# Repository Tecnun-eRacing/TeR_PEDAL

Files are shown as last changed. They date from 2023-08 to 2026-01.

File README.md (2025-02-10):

# TeR_PEDAL
The drivers Input Module Sensor, built to fit FSG rules, it provides the vehicle 
data about:
- Brake Pressure
- APPS (Accelerator Pedal Position Sensor)
- Steering Sensor
## Features
- The module is able to self calibrate itself through a series of commands trough CAN 2.0
- Implausible range detection in all sensors + Safety set-zero
- Storage of calibration values in the internal EEPROM for persistance

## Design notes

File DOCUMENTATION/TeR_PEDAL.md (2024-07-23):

# TeR_PEDAL : Hardware Engineering Report
La placa PEDAL del vehiculo TeR, es la encargada de recopilar todos los inputs que el piloto introduce al coche, Acelerador (APPS), 
Freno Delantero (BPPS) y Volante (STEER). Los datos obtenidos serán utilizados por la ECU para gestionar el par comandado al powertrain.
## Requerimientos
La normativa de FSG tiene una sección (T11.8) que exije los siguientes requerimientos:

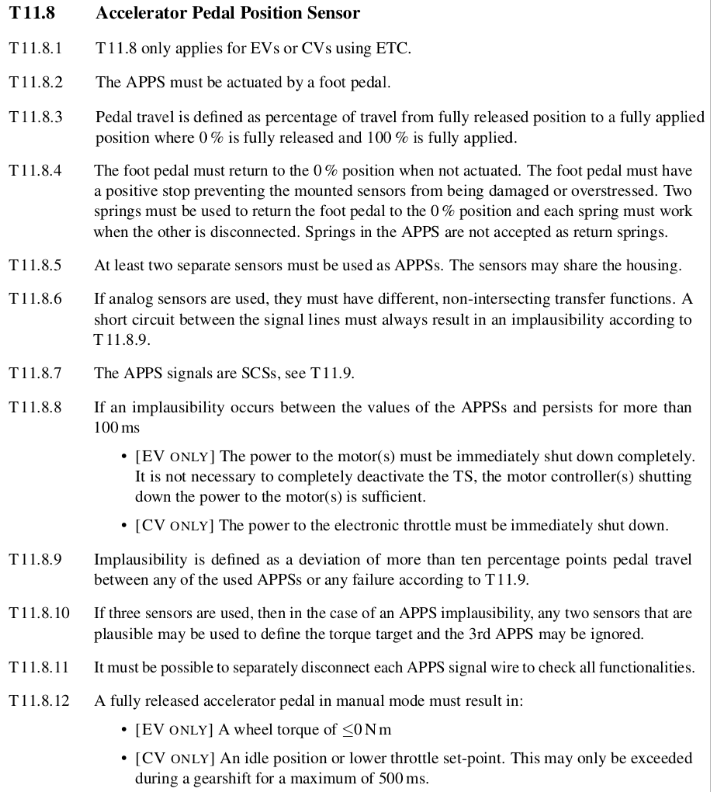
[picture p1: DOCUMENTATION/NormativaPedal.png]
Normativa

## Decisiones

### Sensores
  Por simplicidad y flexibilidad utilizaremos sensores analógicos para la medición de los pedales, steering y freno, cualquier [Potenciometro](https://es.wikipedia.org/wiki/Potenci%C3%B3metro)
  sirve, pero usamos concretamente los VariOhm de Eurosensors

|Fisicamente | Electricamente |
|---|---|
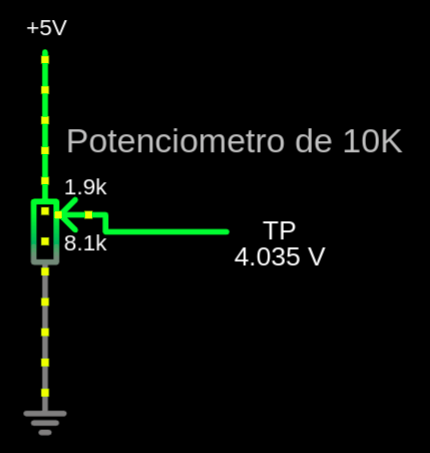
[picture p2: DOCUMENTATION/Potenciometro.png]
Potenciometro
| VariOhm |   |

Para el Freno utilizamos un transductor de Presión-Voltaje que nos permite conocer mediante su función de transferencia la presión en la linea.

### MCU
  Se ha utilizado un stm32F103C8T6 de 48 pines por su facilidad de obtención, versatilidad, disponibilidad de un buen periferico [ADC SAR](https://en.wikipedia.org/wiki/Successive-approximation_ADC) y soporte CAN.
  su uso en la mayoría de placas de baja potencia de procesamiento permite estandarizar y familiarizar todos los diseños donde no se requiere mucha potencia de computo.
  
  | Specification               | Description                          |
  |-----------------------------|--------------------------------------|
  | Core                        | ARM Cortex-M3                        |
  | Operating Frequency         | 72 MHz                               |
  | Flash Memory                | 64 KB                                |
  | RAM                         | 20 KB                                |
  | GPIO                        | 37                                   |
  | Timers                      | 3 x 16-bit, 1 x 32-bit, 2 x watchdog |
  | Communication Interfaces    | 2 x I2C, 3 x USART, 2 x SPI, 1 x USB |
  | ADC                         | 2 x 12-bit, 10-channel               |
  | DAC                         | None                                 |
  | PWM Channels                | 15                                   |
  | Operating Voltage           | 2.0 - 3.6 V                          |
  | Package                     | LQFP48                               |
  | Temperature Range           | -40 to +85 °C                        |
  | Power Consumption (Sleep)   | 2 µA                                 |
  | Debug Interface             | SWD, JTAG                            |
  
  Estos micros se programan muy facilmente mediante el uso de un debugger ST-link y el stm32CUBE-IDE utilizando las librerías [HAL](https://es.wikipedia.org/wiki/Capa_de_abstracci%C3%B3n_de_hardware)

### Filtrado 
Para filtrar las señales recibidas por los sensores se utilizan unos filtros paso bajo RC , pasivos sencillos con frecuencia de corte ~100hz lo cual permite eliminar cualquier señal que 
no provenga del piloto (Sus inputs son mucho más lentos, Fourier...), convendría actualizar a filtros activos utilizando opamps para no afectar las impedancias de entrada.

## Comprobación de requisitos

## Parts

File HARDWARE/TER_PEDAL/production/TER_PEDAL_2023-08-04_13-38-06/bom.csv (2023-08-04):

Designator | Footprint | Quantity | Value | LCSC Part #
C1 | 0805 | 1 | 10u
C10, C9 | 0805 | 2 | 10 µF
C11, C12, C13, C19, C20, C23 | 0603 | 6 | 10u
C14, C17 | 0603 | 2 | 100n
C15, C16 | 0603 | 2 | 10p
C18 | 0603 | 1 | 4.7n
C2, C3, C4, C5 | 0402 | 4 | 100n
C6 | 0402 | 1 | 10n
C7, C8 | 0402 | 2 | 1u
D2 | SOT-23 | 1 | NUP2105L
D3, D4, D5 | 0603 | 3 | LED
F2 | 0805 | 1 | 500ma
FB1, R13, R14, R15 | 0402 | 4 | 120R
J1 | PinHeader_1x04_P2.00mm_Vertical | 1 | DEBUG
J2 | Wuerth_WR-WTB_64800311622_1x03_P1.50mm_Vertical | 1 | APPS_1
J3 | RJ45_Ninigi_GE | 1 | RJ45_Shielded
J4 | Wuerth_WR-WTB_64800311622_1x03_P1.50mm_Vertical | 1 | APPS_2
J5 | Wuerth_WR-WTB_64800311622_1x03_P1.50mm_Vertical | 1 | BPPS_1
J6 | Wuerth_WR-WTB_64800311622_1x03_P1.50mm_Vertical | 1 | SteerSensor
JP1 | PinHeader_1x03_P2.00mm_Vertical | 1 | BOOT0
JP2 | PinHeader_1x03_P2.00mm_Vertical | 1 | BOOT1
JP3 | SolderJumper-3_P1.3mm_Open_Pad1.0x1.5mm | 1 | TermEnable
L1 | IND_TCK-141_TRP | 1 | TCK-141
R10 | 0603 | 1 | 2k
R11 | 0603 | 1 | 4.7k
R12 | 0603 | 1 | 9.1k
R4, R5 | 0603 | 2 | 10k
R6 | 0402 | 1 | 300R
R7 | 0603 | 1 | 100R
R8, R9 | 0603 | 2 | 50R
SW1 | SW_Tactile_SPST_NO_Straight_CK_PTS636Sx25SMTRLFS | 1 | RST
U1 | LQFP-48_7x7mm_P0.5mm | 1 | STM32F103C8Tx
U2 | Converter_DCDC_TRACO_TSR-1_THT | 1 | TSR_1-2450
U3 | SOT-223-3_TabPin2 | 1 | LM1117MP-3.3
U4 | SOIC-8_3.9x4.9mm_P1.27mm | 1 | SN65HVD230
Y1 | Crystal_HC52-6mm_Vertical | 1 | 8mHz

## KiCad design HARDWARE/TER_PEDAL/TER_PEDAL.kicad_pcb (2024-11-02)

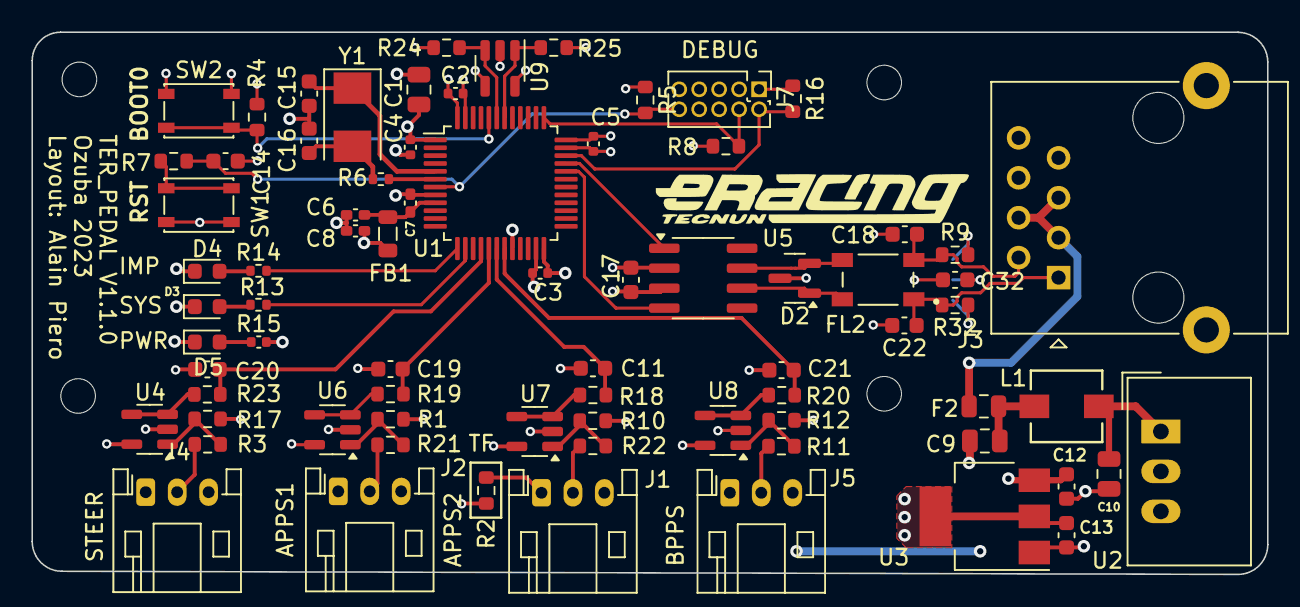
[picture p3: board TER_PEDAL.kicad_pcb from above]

Board: 4 copper layers, 78.6 x 34.5 mm, 80 parts (1 on the bottom side), 48 nets.

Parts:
C1: 10u; C_0805_2012Metric
C2, C3, C4, C5: 100n; C_0402_1005Metric
C6: 10n; C_0402_1005Metric_Pad0.74x0.62mm_HandSolder
C7, C8: 1u; C_0402_1005Metric_Pad0.74x0.62mm_HandSolder
C9, C10: 10 µF; C_0805_2012Metric
C11, C19, C20, C21: 160n; C_0603_1608Metric
C12, C13: 10u; C_0603_1608Metric
C14, C17: 100n; C_0603_1608Metric
C15, C16, C18, C22: 10p; C_0603_1608Metric
C32: 4.7nF; C_0603_1608Metric
D2: NUP2105L; SOT-23
D3: SYS; LED_0603_1608Metric
D4: IMP; LED_0603_1608Metric
D5: PWR; LED_0603_1608Metric
F2: 500ma; Fuse_0805_2012Metric
FB1: 120R; L_0805_2012Metric
FL2: ACT45B-510-2P-TL003; FIL_ACT45B-510-2P-TL003
H1, H2, H3, H4: MountingHole; MountingHole_2.2mm_M2
J1: APPS_2; JST_PH_S3B-PH-K_1x03_P2.00mm_Horizontal
J2, J4: APPS_1; JST_PH_S3B-PH-K_1x03_P2.00mm_Horizontal
J3: RJ45_Shielded; RJ45_Ninigi_GE
J5: BPPS_1; JST_PH_S3B-PH-K_1x03_P2.00mm_Horizontal
J7: DEBUG; PinHeader_2x05_P1.27mm_Vertical
JP2: SolderJumper_3_Open; SolderJumper-3_P1.3mm_Open_Pad1.0x1.5mm
L1: TCK-141; IND_TCK-141_TRP
R1, R10, R12, R17: 9.1k; R_0603_1608Metric
R2: 0R; R_0603_1608Metric
R3, R11, R21, R22: 4.7k; R_0603_1608Metric
R4, R24, R25: 10k; R_0603_1608Metric
R5, R8, R16: 100k; R_0603_1608Metric
R6: 300R; R_0402_1005Metric
R7: 100R; R_0603_1608Metric
R9, R32: 120R; R_0603_1608Metric
R13, R14: 120R; R_0402_1005Metric
R15: 120R; C_0402_1005Metric
R18, R19, R20, R23: 100; R_0603_1608Metric
SW1: RST; SW_SPST_PTS810
SW2: BOOT0; SW_SPST_PTS810
U1: STM32F103C8Tx; LQFP-48_7x7mm_P0.5mm
U2: TSR_1-2450; Converter_DCDC_TRACO_TSR-1_THT
U3: LM1117MP-3.3; SOT-223-3_TabPin2
U4, U6, U7, U8: LM321; SOT-23-5
U5: TCAN332; SOIC-8_3.9x4.9mm_P1.27mm
U9: AT24CS02-STUM; SOT-23-5
Y1: 8mHz; Crystal_SMD_5032-2Pin_5.0x3.2mm

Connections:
+3.3V: C1.1, C2.1, C3.1, C4.1, C5.1, C8.1, C13.1, C17.2, FB1.2, J7.1 (VTref), R5.1, R15.2, R16.1, R24.1, R25.1, SW2.2 (B), U1.1 (VBAT), U1.24 (VDD), U1.36 (VDD), U1.48 (VDD), U3.2 (VO), U4.5 (V+), U5.3 (VCC), U6.5 (V+), U7.5 (V+), U8.5 (V+), U9.4 (VCC)
+3.3VADC: C6.1, C7.1, FB1.1, U1.9 (VDDA)
+5V: C12.1, J2.1, J4.1, J5.1, R2.1, U2.3 (Vout), U3.3 (VI)
+24V: F2.1, J3.3, J3.4, J3.5
/CAN/CAN+: C18.2, FL2.2, J3.2, R9.1
/CAN/CAN-: C22.1, FL2.1, J3.1, R32.2
/CAN/CAN_RX: U1.32 (PA11), U5.4 (RXD)
/CAN/CAN_TX: U1.33 (PA12), U5.1 (TXD)
/CAN/can+: D2.2 (K), FL2.3, U5.7 (CANH)
/CAN/can-: D2.1 (K), FL2.4, U5.6 (CANL)
/EEPROM/SCL: R25.2, U1.42 (PB6), U9.1 (SCL)
/EEPROM/SDA: R24.2, U1.43 (PB7), U9.3 (SDA)
/IMP_LED: R14.2, U1.13 (PA3)
/MICRO/APPS_1_ADC: C19.1, R19.2, U1.17 (PA7)
/MICRO/APPS_2_ADC: C11.1, R18.2, U1.18 (PB0)
/MICRO/BOOT0: R4.1, SW2.1 (A), U1.44 (BOOT0)
/MICRO/BPPS_ADC: C21.1, R20.2, U1.19 (PB1)
/MICRO/NRST: C14.1, J7.10 (~RESET), R5.2, R7.2, U1.7 (NRST)
/MICRO/OSC_IN: C15.2, U1.5 (PD0), Y1.1
/MICRO/OSC_OUT: R6.1, U1.6 (PD1)
/MICRO/STEER_ADC: C20.1, R23.2, U1.16 (PA6)
/MICRO/SWCLK: J7.4 (SWCLK/TCK), R8.1, U1.37 (PA14)
/MICRO/SWDIO: J7.2 (SWDIO/TMS), R16.2, U1.34 (PA13)
/SENSORS/Brake: J5.2, R11.1
/SENSORS/SENS_1: J2.2, R21.2
/SENSORS/SENS_2: J1.2, R22.2
/SYS: R13.2, U1.14 (PA4)
GND: C1.2, C2.2, C3.2, C4.2, C5.2, C6.2, C7.2, C8.2, C9.2, C10.2, C11.2, C12.2, C13.2, C14.2, C15.1, C16.2, C17.1, C18.1, C19.2, C20.2, C21.2, C22.2, C32.2, D2.3 (A), D3.1 (K), D4.1 (K), D5.1 (K), J1.3, J2.3, J3.6, J3.7, J3.8, J3.SH, J4.3, J5.3, J7.3 (GND), J7.5 (GND), J7.9 (GNDDetect), R1.1, R4.2, R8.2, R10.1, R12.2, R17.1, SW1.1 (A), U1.8 (VSSA), U1.20 (PB2), U1.23 (VSS), U1.35 (VSS), U1.47 (VSS), U2.2 (GND), U3.1 (GND), U4.2 (V-), U5.2 (GND), U6.2 (V-), U7.2 (V-), U8.2 (V-), U9.2 (GND), U9.5 (WP)
unnamed: C9.1, F2.2, L1.2
unnamed: C16.1, R6.2, Y1.2
unnamed: D3.2 (A), R13.1
unnamed: D4.2 (A), R14.1
unnamed: D5.2 (A), R15.1
unnamed: J1.1, R2.2
unnamed: J4.2, R3.2
unnamed: JP2.1 (A), R9.2
unnamed: JP2.3 (B), R32.1
unnamed: C32.1, JP2.2 (C)
unnamed: R7.1, SW1.2 (B)
unnamed: C10.1, L1.1, U2.1 (Vin)
unnamed: R3.1, R17.2, U4.1 (+)
unnamed: R23.1, U4.3 (-), U4.4
unnamed: R1.2, R21.1, U6.1 (+)
unnamed: R19.1, U6.3 (-), U6.4
unnamed: R10.2, R22.1, U7.1 (+)
unnamed: R18.1, U7.3 (-), U7.4
unnamed: R11.2, R12.1, U8.1 (+)
unnamed: R20.1, U8.3 (-), U8.4

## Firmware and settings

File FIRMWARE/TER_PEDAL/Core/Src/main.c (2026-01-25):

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
/* Includes ------------------------------------------------------------------*/
#include "main.h"
#include "adc.h"
#include "can.h"
#include "dma.h"
#include "i2c.h"
#include "tim.h"
#include "gpio.h"

/* USER CODE BEGIN Includes */
#include "TeR_CAN.h" //Master libray
#include "pedal.h" //Board functions Library
/* USER CODE END Includes */


/* USER CODE BEGIN PV */
EE24_HandleTypeDef ee24;

//Mensajes

/* USER CODE END PV */

void SystemClock_Config(void);
static void MX_NVIC_Init(void);
/* USER CODE BEGIN PFP */
void readSensors(void); //Lectura de todos los sensores

/* USER CODE END PFP */

/**
 * @brief  The application entry point.
 * @retval int
 */
int main(void) {

	/* MCU Configuration--------------------------------------------------------*/

	/* Reset of all peripherals, Initializes the Flash interface and the Systick. */
	HAL_Init();

	/* Configure the system clock */
	SystemClock_Config();

	/* Initialize all configured peripherals */
	MX_GPIO_Init();
	MX_DMA_Init();
	MX_ADC1_Init();
	MX_CAN_Init();
	MX_TIM2_Init();
	MX_I2C1_Init();

	/* Initialize interrupts */
	MX_NVIC_Init();
	/* USER CODE BEGIN 2 */
	EE24_Init(&ee24, &hi2c1, EE24_ADDRESS_DEFAULT);
	initPedal(&hadc1); //Carga los offsets en la placa y arranca enganchada al adc1
	initCAN(&hcan, &htim2); //Arranca el can enganchado a el timer 2
	/* USER CODE END 2 */

	/* Infinite loop */
	/* USER CODE BEGIN WHILE */
	while (1) {
		; //Good code depends just on interruptions : )
		/* USER CODE END WHILE */

		/* USER CODE BEGIN 3 */
	}
	/* USER CODE END 3 */
}

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


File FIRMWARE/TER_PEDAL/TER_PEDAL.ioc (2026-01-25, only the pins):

Mcu.UserName=STM32F103C8Tx
PA11.Signal=CAN_RX
PA12.Signal=CAN_TX
PA13.Signal=SYS_JTMS-SWDIO
PA14.Signal=SYS_JTCK-SWCLK
PA3.GPIO_Label=IMP_LED
PA3.Signal=GPIO_Output
PA4.GPIO_Label=SYS
PA4.Signal=GPIO_Output
PA6.GPIO_Label=STEER
PA6.Signal=ADCx_IN6
PA7.GPIO_Label=APPS_1
PA7.Signal=ADCx_IN7
PB0.GPIO_Label=APPS_2
PB0.Signal=ADCx_IN8
PB1.GPIO_Label=BPPS
PB1.Signal=ADCx_IN9
PB6.Signal=I2C1_SCL
PB7.Signal=I2C1_SDA
PD0-OSC_IN.Signal=RCC_OSC_IN
PD1-OSC_OUT.Signal=RCC_OSC_OUT

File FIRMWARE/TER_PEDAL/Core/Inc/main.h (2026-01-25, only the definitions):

#define IMP_LED_Pin GPIO_PIN_3
#define IMP_LED_GPIO_Port GPIOA
#define SYS_Pin GPIO_PIN_4
#define SYS_GPIO_Port GPIOA
#define STEER_Pin GPIO_PIN_6
#define STEER_GPIO_Port GPIOA
#define APPS_1_Pin GPIO_PIN_7
#define APPS_1_GPIO_Port GPIOA
#define APPS_2_Pin GPIO_PIN_0
#define APPS_2_GPIO_Port GPIOB
#define BPPS_Pin GPIO_PIN_1
#define BPPS_GPIO_Port GPIOB

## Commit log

2023-05-01 Added kicad project, began mcu design and power stage DCDC converters
    [MICRO.kicad_sch, POWER.kicad_sch, TER_PEDAL.kicad_pcb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]
2023-05-01 Added STM32 related Application notes and datasheet
2023-05-01 Added Can transceiver Circuit
    [CAN.kicad_sch, TER_PEDAL.kicad_sch]
2023-05-01 Added Uniport, Debug and began sensors design
    [CAN.kicad_sch, MICRO.kicad_sch, SENSORS.kicad_sch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]
2023-05-02 Added Sensors PSU
    [POWER.kicad_sch, SENSORS.kicad_sch]
2023-05-02 Added footprints to existing components
    [CAN.kicad_sch, MICRO.kicad_sch, POWER.kicad_sch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]
2023-05-04 Finished Initial Schematic
    [MICRO.kicad_sch, SENSORS.kicad_sch, TER_PEDAL.kicad_sch]
2023-05-04 Started Layout and fixed wrong footprints
    [MICRO.kicad_sch, POWER.kicad_sch, SENSORS.kicad_sch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]
2023-05-05 Sized and Fixed even more footprints + Initial layout
    [CAN.kicad_sch, MICRO.kicad_sch, POWER.kicad_sch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]
2023-05-05 Added Eracing Logo
    [SENSORS.kicad_sch, TER_PEDAL.kicad_pcb]
2023-05-09 Began layout and switched to 4 layer board
    [POWER.kicad_sch, TER_PEDAL.kicad_pcb, TER_PEDAL.kicad_sch]
2023-05-09 added powerplanes
    [TER_PEDAL.kicad_pcb]
2023-05-12 Initial Layout Finished
    [MICRO.kicad_sch, TER_PEDAL.kicad_pcb]
2023-05-16 Changed Pinout and added status leds silkmask
    [TER_PEDAL.kicad_pcb]
2023-05-18 Added new Database Formats and started ADC troubleshooting
2023-05-19 Added ADC multichannel DMA reads+ APPS Implausability
2023-05-30 Changed code generation options for clarity in main.c and added virtual eeprom library for storing calibration values of the pedals
2023-06-05 Added Rx Message interupt handling and calibration command
2023-06-07 Switched Imp flag to the one from ter dbc and added brake calibration commands
2023-06-07 Fixed bugs and added implausability reset cmd
    [main.c]
2023-08-03 Swapped Custom Supply for traco for simplicity
    [MICRO.kicad_sch, POWER.kicad_sch, TER_PEDAL.kicad_pcb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]
2023-08-03 Added decouple to all sensors and a new steering sensor input
    [MICRO.kicad_sch, SENSORS.kicad_sch, TER_PEDAL.kicad_sch]
2023-08-03 The RJ45 pinout was incorrect according to the poe standard, started redesign and relocation of the board revision
    [TER_PEDAL.kicad_pcb, UNIPORT.kicad_sch]
2023-08-04 Rearranged board
    [MICRO.kicad_sch, SENSORS.kicad_sch, TER_PEDAL.kicad_pcb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]
2023-08-10 Added holes, connectors and finished re-layout
    [SENSORS.kicad_sch, TER_PEDAL.kicad_pcb, TER_PEDAL.kicad_sch]
2023-08-11 Finished Routing for redisign
    [MICRO.kicad_sch, TER_PEDAL.kicad_pcb]
2023-08-18 Added Labels on silkscreen and, versioning and IMG
    [TER_PEDAL.kicad_pcb]
2023-08-21 Fixed ferrite bead imposible size to 805
    [TER_PEDAL.kicad_pcb, bom.csv, designators.csv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]
2023-09-02 Quick Fix on the debug conector Bus where it was not connected to 3.3V + Labels
    [MICRO.kicad_sch, TER_PEDAL.kicad_pcb]
2023-09-03 Adapted Code to V1.0.0 board
2023-09-17 Bumped Bugfix version and fixed unnecessary BOOT0 pin and rj45 placement
    [MICRO.kicad_sch, TER_PEDAL.kicad_pcb]
2023-09-27 Fixed bug with ADC conversion where it would not Read properly any signal cause of the addition of steer and forgetting to include it in conversion
    [TER_PEDAL.ioc, main.c]
2023-10-06 Removed the possibility of the micro entering Error_Handler instead an error in can transmission results in the DBG led turning on
    [TER_PEDAL.ioc, main.c]
2023-10-29 Accurate rj45 3d model
    [TER_PEDAL.kicad_pcb]
2023-11-24 Added pull down resistors for adc to prevent floating value when disconnected signals, added LABELS lots of labels
    [SENSORS.kicad_sch, TER_PEDAL.kicad_pcb]
2023-11-24 Added Template to Schematics
    [TER_PEDAL.kicad_sch]
2023-11-28 Added Pulldown simulation
    [SENSORS.kicad_sch]
2023-12-12 Corrected inputs in code, added steering autocal and verified that calibration sequence works
    [main.c]
2023-12-21 Added default value to flash writing if new board, corrected multiple bugs with calibration
    [main.c]
2024-06-05 condensador señal brake
    [CAN.kicad_sch, MICRO.kicad_sch, POWER.kicad_sch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]
2024-07-25 Cabiado esquematico, falta layout
    [CAN.kicad_sch, MICRO.kicad_sch, SENSORS.kicad_sch]
2024-07-26 Hecho layout
    [TER_PEDAL.kicad_pcb]
2024-07-26 Quick float math fix
    [TER_PEDAL.ioc, TeR_CAN.c, main.h]
2024-07-26 Ane y el algebra de BOOL
2024-07-29 Update pedal.h
    Cambio Epiko del limite de implausability
2024-08-16 Added voltage followers to sensing, improved can circuitri, improved layout, waiting for routing
    [CAN.kicad_sch, MICRO.kicad_sch, POWER.kicad_sch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]
2024-09-04 Alimentacion de los sensores de la apps actualizado a 5V
    [SENSORS.kicad_sch]
2024-10-04 çMejorado layout
    [CAN.kicad_sch, SENSORS.kicad_sch, TER_PEDAL.kicad_pcb]
2024-10-21 avanzando layout
    [CAN.kicad_sch, TER_PEDAL.kicad_pcb]
2024-10-22 Añadiendo eeprom (no terminado)
    [EEPROM.kicad_sch, MICRO.kicad_sch, TER_PEDAL.kicad_pcb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]
2024-10-22 EEPROM añadida
    [EEPROM.kicad_sch]
2024-11-02 conectores mas dentro, relayout can
    [TER_PEDAL.kicad_pcb]
2025-02-10 Better gitignored
    [bom.csv, designators.csv, positions.csv]
2026-03-11 Not working code for steering disconnect
    [pedal.c]
2026-04-07 working code for steering disconnect :)

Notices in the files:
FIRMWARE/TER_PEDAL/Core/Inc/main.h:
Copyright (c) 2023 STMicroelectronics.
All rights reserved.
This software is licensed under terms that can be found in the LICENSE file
